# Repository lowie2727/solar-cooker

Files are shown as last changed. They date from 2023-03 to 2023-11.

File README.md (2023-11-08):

# Solar cooker

This repository contains the [arduino code](arduino) and [pcb layout](kicad) for the testing station of our solar cooker.

# Contributing

This repository is no longer actively maintained. If you want to contribute to this project, you can always fork this repository.

# Final result

This is the test station built by the first generation of electronics students.

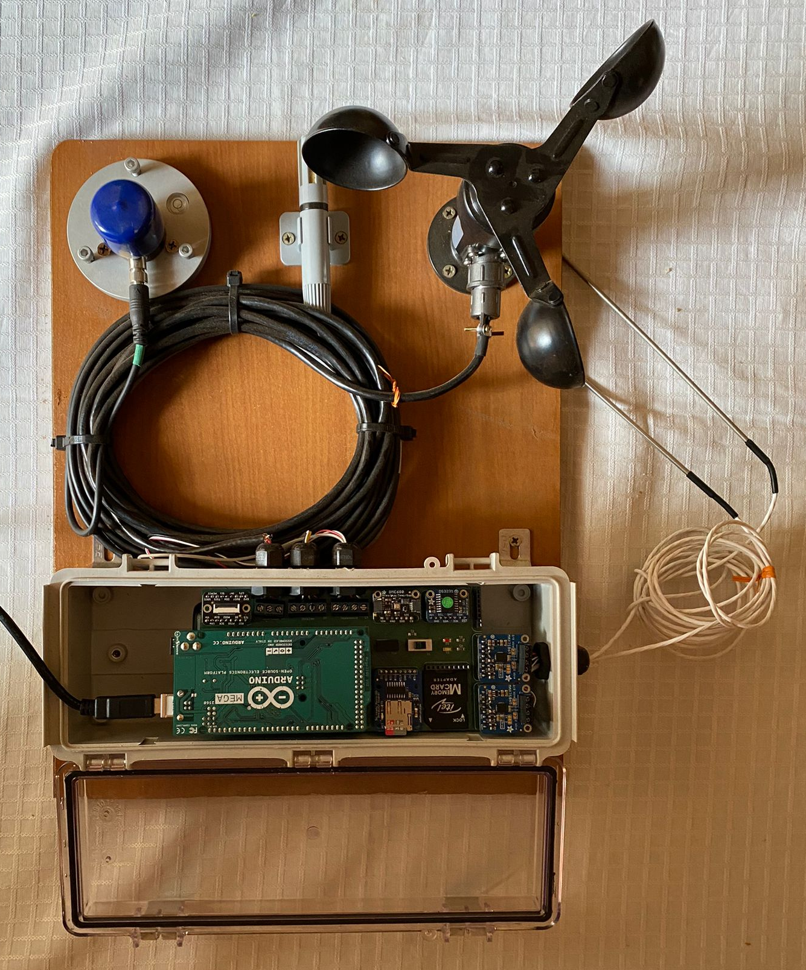
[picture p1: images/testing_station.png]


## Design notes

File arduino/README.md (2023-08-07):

# Arduino

The [**src**](src) folder contains the code for both the individual components and the code for the entire testing station.

The folder [**src/main**](src/main) contains the various components brought together. Each component has its own cpp file except for the LCD screen and microSD module. It is joined via header files in [main.cpp](src/main/main.cpp).

In the [**src/components**](src/components) subfolder, you will find code for each individual component, along with the connection diagram.

## PlatformIO

We migrated from the [Arduino IDE](https://www.arduino.cc/en/software) to [PlatformIO](https://platformio.org/platformio-ide) because of the size of the project.

### Prerequisites

#### Visual Studio Code

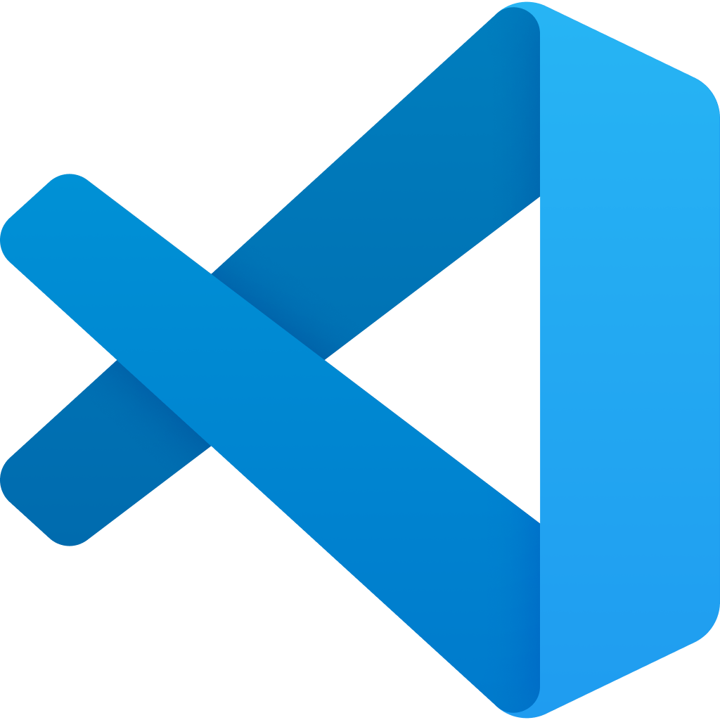
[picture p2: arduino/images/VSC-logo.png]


To use PlatformIO u need to first install [Visual Studio Code](https://code.visualstudio.com/)

When VSCode is installed you need to install the [PlatformIO extension](https://platformio.org/install/ide?install=vscode) in VSCode and then you are ready to compile. It may take some time so be patient.

#### Copy the project to your computer

To copy the project to your local machine you can download this [zip](https://github.com/lowie2727/solar-cooker/archive/refs/heads/main.zip) or if you have git installed you can run the `git clone https://github.com/lowie2727/solar-cooker.git` in a folder of your choice. Git is recommended to get the latest updates to the project.

### Using PlatformIO

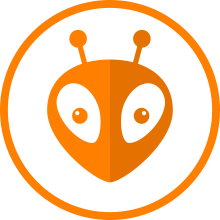
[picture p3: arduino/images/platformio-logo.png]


#### Opening the PlatformIO project

When the extension is successfully installed, you will get a new icon on the left in VSCode. Click on it and open the correct folder (open the folder with the platform.ini file assuming you already have a local copy of the project on your computer). In this case open the [arduino](/arduino) folder.

#### Build main

You will now see several project tasks when you click on the PlatformIO logo, open main and click on build. The terminal will open, if everything worked out it should show SUCCESS when it is done.

#### Upload and Monitor

To upload the code and view the serial monitor, a button is provided.

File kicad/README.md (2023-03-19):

# KiCad

## Installation

please install the latest kicad version from [kicad.org](https://www.kicad.org/download/)

## CADLAB (visual version control)
View this project on [CADLAB.io](https://cadlab.io/project/26616)

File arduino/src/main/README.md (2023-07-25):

# Main

## CSV

CSV files are generated in the following folder structure: YYYY/MM/DDHHMMSS.csv

the header of the CSV file looks like this:

| Year | Month | Day | Hour | Minute | Second | Outside temperature [°C] | Wind speed [m/s] | Air pressure (inside box) [hPa] | Relative humidity (inside box) [%] | Temperature inside pot 1 [°C] | Temperature inside pot 2 [°C] | Temperature inside pot 3 [°C] | Solar irradiance [W/m²] |
|---|---|-----|---|---|---|---|---|---|---|---|---|---|---|

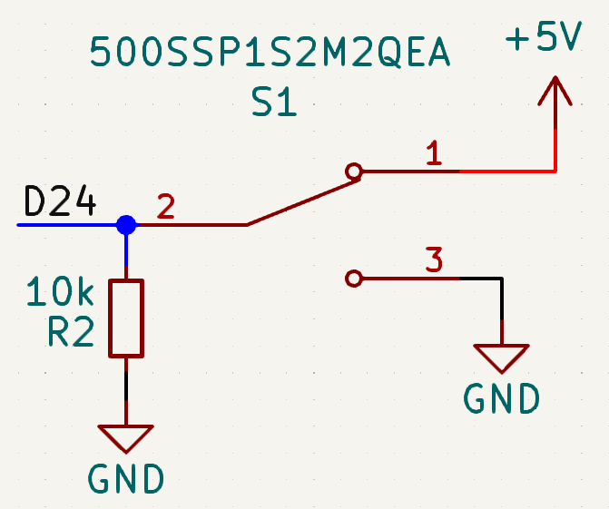
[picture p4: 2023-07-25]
arduino/src/components/switch/images/pinout_switch.png

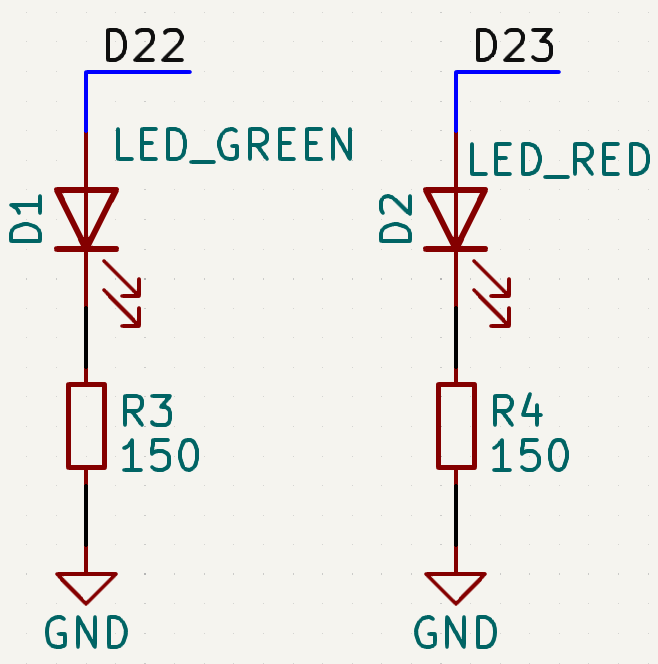
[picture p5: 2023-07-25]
arduino/src/components/switch/images/pinout_LED.png

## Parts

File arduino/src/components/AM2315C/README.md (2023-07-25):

# Sources

- [learn.adafruit.com](https://learn.adafruit.com/adafruit-aht20)

# Dependencies

- [Adafruit AHTX0](https://github.com/adafruit/Adafruit_AHTX0)

# Schematic

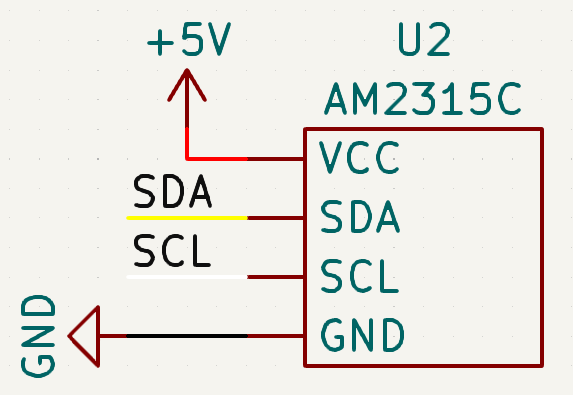
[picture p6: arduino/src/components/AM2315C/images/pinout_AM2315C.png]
pinout


## I2C

| Pin | Uno | Mega |
| --- | --- | ---- |
| SDA | SDA | 20 |
| SCL | SCL | 21 |

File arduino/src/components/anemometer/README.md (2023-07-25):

# Sources

- [wiki.dfrobot.com](https://wiki.dfrobot.com/Wind_Speed_Sensor_Voltage_Type_0-5V__SKU_SEN0170)

# Schematic

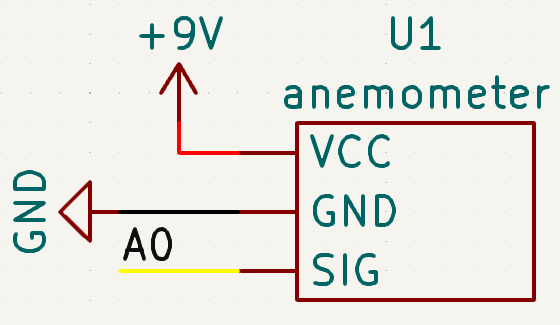
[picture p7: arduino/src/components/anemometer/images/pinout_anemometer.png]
pinout


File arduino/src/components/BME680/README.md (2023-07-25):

# Sources

- [learn.adafruit.com](https://learn.adafruit.com/adafruit-bme680-humidity-temperature-barometic-pressure-voc-gas)

# Dependencies

- [Adafruit BME680 Library](https://github.com/adafruit/Adafruit_BME680)

# Schematic

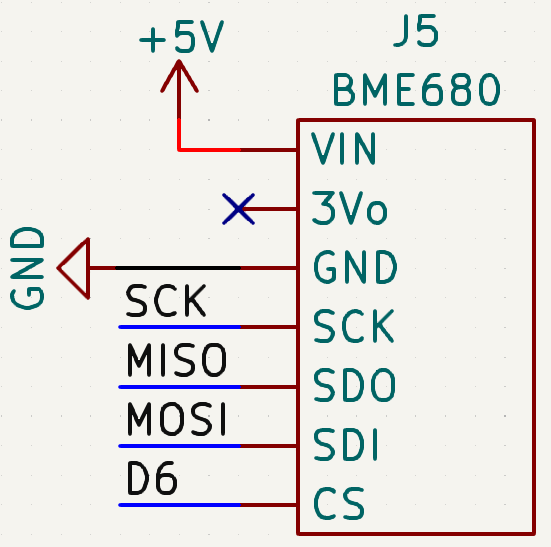
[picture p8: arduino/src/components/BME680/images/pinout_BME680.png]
pinout


## SPI

| Pin  | Uno | Mega |
| ---- | --- | ---- |
| MISO | 11  | 50 |
| MOSI | 12  | 51 |
| SCK  | 13  | 52 |

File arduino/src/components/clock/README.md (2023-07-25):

# Sources

- [learn.adafruit.com](https://learn.adafruit.com/adafruit-ds3231-precision-rtc-breakout)

# Dependencies

- [RTClib](https://github.com/adafruit/RTClib)

# Schematic

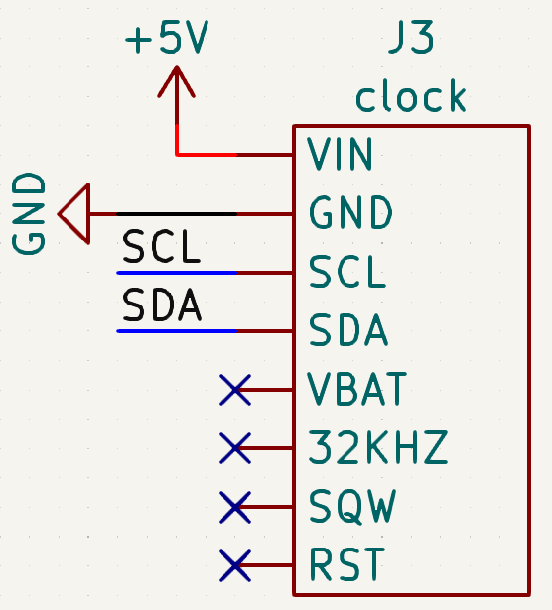
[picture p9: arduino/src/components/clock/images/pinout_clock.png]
pinout


## I2C

| Pin | Uno | Mega |
| --- | --- | ---- |
| SDA | SDA | 20 |
| SCL | SCL | 21 |

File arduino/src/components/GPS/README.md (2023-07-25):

# Sources

- [learn.adafruit.com](https://learn.adafruit.com/adafruit-ultimate-gps)

# Dependencies

- [Adafruit GPS Library](https://github.com/adafruit/Adafruit_GPS)

# Schematic

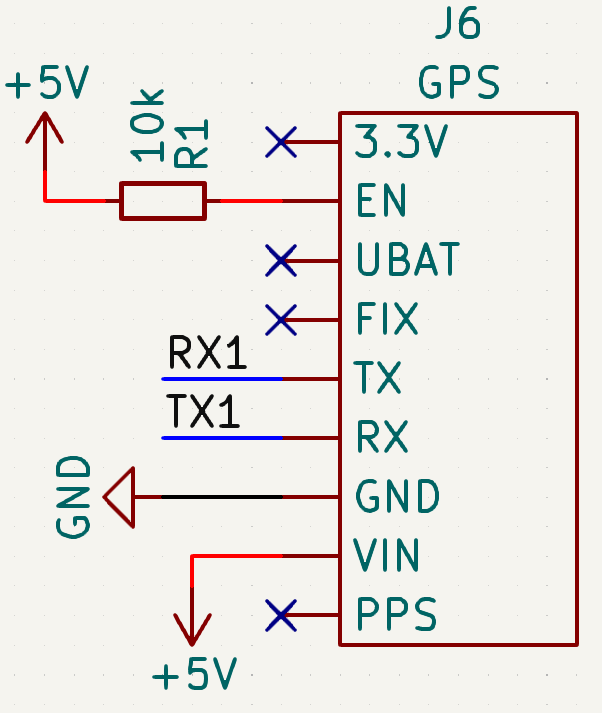
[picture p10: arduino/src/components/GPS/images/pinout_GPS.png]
pinout


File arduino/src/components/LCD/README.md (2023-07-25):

# Sources

- [learn.adafruit.com](https://learn.adafruit.com/2-2-tft-display)

# Dependencies

- [Adafruit ILI9341](https://github.com/adafruit/Adafruit_ILI9341)

# Schematic

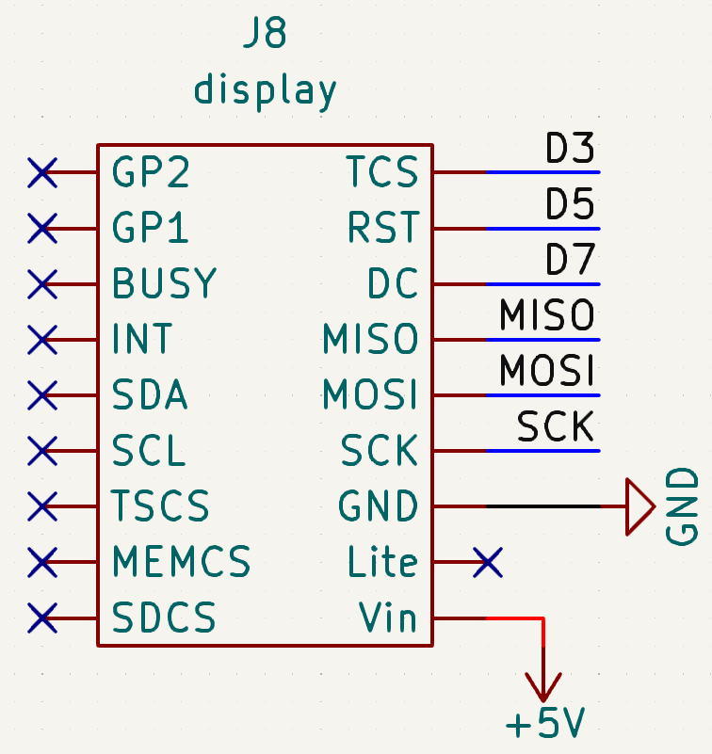
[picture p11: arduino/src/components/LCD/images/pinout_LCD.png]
pinout


## SPI

| Pin  | Uno | Mega |
| ---- | --- | ---- |
| MISO | 11  | 50 |
| MOSI | 12  | 51 |
| SCK  | 13  | 52 |

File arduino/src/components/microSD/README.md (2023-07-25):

# Sources

- [learn.adafruit.com](https://learn.adafruit.com/adafruit-micro-sd-breakout-board-card-tutorial)

# Dependencies

- [SdFat](https://github.com/greiman/SdFat)

# Schematic

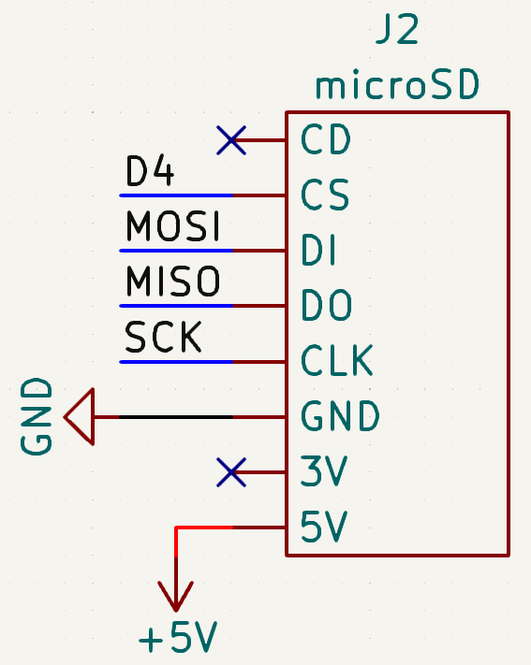
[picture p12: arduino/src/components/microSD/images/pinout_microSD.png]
pinout


## SPI

| Pin  | Uno | Mega |
| ---- | --- | ---- |
| MISO | 11  | 50 |
| MOSI | 12  | 51 |
| SCK  | 13  | 52 |

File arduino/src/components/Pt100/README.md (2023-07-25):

# Sources

- [learn.adafruit.com](https://learn.adafruit.com/adafruit-max31865-rtd-pt100-amplifier)

# Dependencies

- [Adafruit MAX31865 library](https://github.com/adafruit/Adafruit_MAX31865)

# Schematic

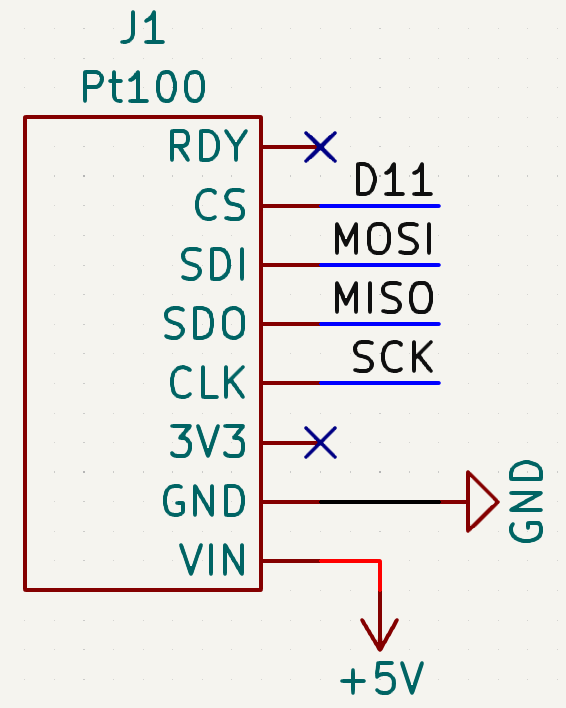
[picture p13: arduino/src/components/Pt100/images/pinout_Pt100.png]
pinout


## SPI

| Pin  | Uno | Mega |
| ---- | --- | ---- |
| MISO | 11  | 50 |
| MOSI | 12  | 51 |
| SCK  | 13  | 52 |

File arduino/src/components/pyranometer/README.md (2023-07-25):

# Sources

- [apogeeinstruments.com](https://www.apogeeinstruments.com/sp-215-ss-amplified-0-5-volt-pyranometer)

# Schematic

pinout

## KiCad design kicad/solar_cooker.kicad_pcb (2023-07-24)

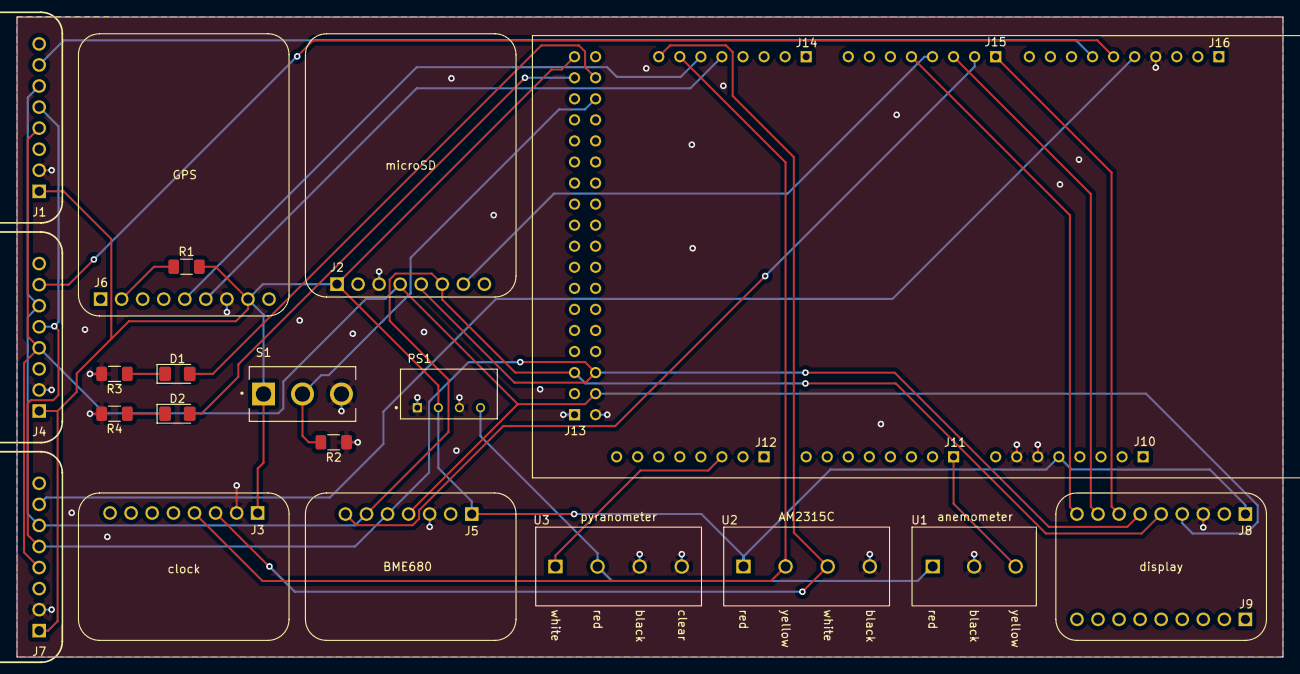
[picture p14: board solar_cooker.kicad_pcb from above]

Board: 2 copper layers, 152.7 x 77.2 mm, 20 parts (1 on the bottom side), 26 nets.

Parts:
A1: A000067; ARDUINO_A000067
D1: LED_GREEN; LED_1206_3216Metric_Pad1.42x1.75mm_HandSolder
D2: LED_RED; LED_1206_3216Metric_Pad1.42x1.75mm_HandSolder
J1, J4, J7: Pt100
J2: microSD
J3: clock
J5: BME680
J6: GPS
J8: display
PS1: TBA_1-0519; CONV_TBA_1-0519
R1, R2: 10k; R_1206_3216Metric_Pad1.30x1.75mm_HandSolder
R3, R4: 150; R_1206_3216Metric_Pad1.30x1.75mm_HandSolder
S1: 500SSP1S2M2QEA; SW_500SSP1S2M2QEA
U1: anemometer; screw_terminal_3pin
U2: AM2315C; screw_terminal_4pin
U3: pyranometer; screw_terminal_4pin

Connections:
+5V: A1.5V_1 (+5V_1), A1.5V_3 (+5V_3), J1.1 (VIN), J2.1 (5V), J3.1 (VIN), J4.1 (VIN), J5.1 (VIN), J6.8 (VIN), J7.1 (VIN), J8.1 (Vin), PS1.2 (+VIN(VCC)), R1.2, S1.1, U2.1 (VCC)
+9V: PS1.4 (+VOUT), U1.1 (VCC), U3.2 (VCC)
/A0: A1.AD0, U1.3 (SIG)
/A10: A1.AD10, U3.1 (SIG)
/D3: A1.3, J8.9 (TCS)
/D4: A1.4, J2.7 (CS)
/D5: A1.5, J8.8 (RST)
/D6: A1.6, J5.7 (CS)
/D7: A1.7, J8.7 (DC)
/D11: A1.11, J1.7 (CS)
/D12: A1.12, J4.7 (CS)
/D13: A1.13, J7.7 (CS)
/D22: A1.22, D1.2 (A)
/D23: A1.23, D2.2 (A)
/D24: A1.24, R2.2, S1.2
/MISO: A1.50, J1.5 (SDO), J2.5 (DO), J4.5 (SDO), J5.5 (SDO), J7.5 (SDO), J8.6 (MISO)
/MOSI: A1.51, J1.6 (SDI), J2.6 (DI), J4.6 (SDI), J5.6 (SDI), J7.6 (SDI), J8.5 (MOSI)
/RX1: A1.19, J6.5 (TX)
/SCK: A1.52, J1.4 (CLK), J2.4 (CLK), J4.4 (CLK), J5.4 (SCK), J7.4 (CLK), J8.4 (SCK)
/SCL: A1.21, J3.3 (SCL), U2.3 (SCL)
/SDA: A1.20, J3.4 (SDA), U2.2 (SDA)
/TX1: A1.18, J6.6 (RX)
GND: A1.GND1, A1.GND2, A1.GND3, A1.GND4, A1.GND5, J1.2 (GND), J2.3 (GND), J3.2 (GND), J4.2 (GND), J5.3 (GND), J6.7 (GND), J7.2 (GND), J8.3 (GND), PS1.1 (-VIN(GND)), PS1.3 (-VOUT), R2.1, R3.2, R4.2, S1.3, U1.2 (GND), U2.4 (GND), U3.3 (GND), U3.4 (GND)
unnamed: D1.1 (K), R3.1
unnamed: D2.1 (K), R4.1
unnamed: J6.2 (EN), R1.1

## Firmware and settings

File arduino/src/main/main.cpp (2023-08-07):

#include <Arduino.h>

#include "anemometer.h"

#include "AM2315C.h"

#include "BME680.h"

#include "clock.h"

#include "Pt100.h"

#include "pyranometer.h"

#include "switch.h"

// LCD
void LCDSetup();

#include "Adafruit_GFX.h"
#include "Adafruit_ILI9341.h"
#include "SPI.h"

#define TFT_DC 7
#define TFT_CS 3
#define TFT_RST 5

Adafruit_ILI9341 tft = Adafruit_ILI9341(TFT_CS, TFT_DC, TFT_RST);

void writeLine1();
void writeLine2();
void writeLine3();
void writeLine4();
void writeLine5();
void writeLine6();
void writeLine7();
void writeLine8();
void writeLine9();

char previousLine1[100];
char previousLine2[100];
char previousLine3[100];
char previousLine4[100];
char previousLine5[100];
char previousLine6[100];
char previousLine7[100];
char previousLine8[100];
char previousLine9[100];

float previousTemp = -1;
float previousHumidity = -1;
float previousPt100Temp1 = -1;
float previousPt100Temp2 = -1;
float previousPt100Temp3 = -1;
uint8_t previousSecond = -1;
float previousWind = -1;
float previousSolarIrradiance = -1;
float previousSlope = -1;

void writeDataToScreen();

unsigned long previousMillisScreen = 0;

// SD
#include <SdFat.h>

const int chipSelect = 4;

SdFat sd;
SdFile myFile;

char filePath[200];
int fileNameUpdated = 0;
unsigned long previousMillisSD = 0;

void updateFileName();
void makeFile();

void microSDSetup();
void writeCSVHeaders();
void writeDataToSD();

float tempBuffer[60];
int bufferIndex = 0;
int isArrayEmpty = 1;

void shiftAndAppend(float array[], float value);
void initArray(float array[], float value);

unsigned long testDurationMillis = 0;

void setup() {
  Serial.begin(9600);
  while (!Serial) {
  }
  Serial.println();

  AM2315CSetup();
  anemoSetup();
  BME680Setup();
  clockSetup();
  microSDSetup();
  Pt100Setup();
  pyranoSetup();
  switchSetup();
  LCDSetup();
}

void loop() {
  if (getSwitchState()) {
    greenLedOn();

    if (!fileNameUpdated) {
      testDurationMillis = millis();
      updateFileName();
      writeCSVHeaders();
      fileNameUpdated = 1;
    }

    unsigned long currentMillisScreen = millis();

    if (currentMillisScreen - previousMillisScreen >= 1000) {
      writeDataToScreen();
      previousMillisScreen = currentMillisScreen;
    }

    unsigned long currentMillisSD = millis();

    if (currentMillisSD - previousMillisSD >= 10000) {
      writeDataToSD();
      previousMillisSD = currentMillisSD;
    }
  } else {
    redLedOn();
    fileNameUpdated = 0;
    isArrayEmpty = 1;
  }
}

void microSDSetup() {
  if (!sd.begin(chipSelect, SPI_FULL_SPEED)) {
    sd.initErrorHalt();
  }
}

void writeCSVHeaders() {
  char CSVHeaders[] =
      "Year;Month;Day;Hour;Minute;Second;Outside temperature "
      "[°C];Wind speed [m/s];Air pressure (inside box) [hPa];Relative humidity "
      "(inside box) [%];Temperature inside pot 1 [°C];Temperature inside pot 2 "
      "[°C];Temperature inside pot 3 [°C];Solar irradiance [W/m²]";
  if (!myFile.open(filePath, O_RDWR | O_CREAT | O_AT_END)) {
    sd.errorHalt(F("opening test.txt for write failed"));
  }
  Serial.println("Writing CSV headers");
  myFile.println(CSVHeaders);
  myFile.close();
  Serial.println(F("done writing."));
}

void writeDataToSD() {
  char AM2315CTemp[30];
  dtostrf(getAM2315CTemp(), 4, 2, AM2315CTemp);

  char AM2315CHum[20];
  dtostrf(getAM2315CHum(), 5, 2, AM2315CHum);

  char BME680Humidity[20];
  dtostrf(getBME680Humidity(), 6, 2, BME680Humidity);

  char BME680Pressure[20];
  dtostrf(getBME680Pressure(), 6, 2, BME680Pressure);

  char BME680Temperature[20];
  dtostrf(getBME680Temperature(), 6, 2, BME680Temperature);

  char windSpeed[20];
  dtostrf(getWindSpeed(), 4, 2, windSpeed);

  char Pt100Temp1[20];
  if (!getPt100Fault_1()) {
    dtostrf(getPt100Temp1(), 5, 2, Pt100Temp1);
  } else {
    snprintf(Pt100Temp1, 20, "x");
  }

  char Pt100Temp2[20];
  if (!getPt100Fault_2()) {
    dtostrf(getPt100Temp2(), 5, 2, Pt100Temp2);
  } else {
    snprintf(Pt100Temp2, 20, "x");
  }

  char Pt100Temp3[20];
  if (!getPt100Fault_3()) {
    dtostrf(getPt100Temp3(), 5, 2, Pt100Temp3);
  } else {
    snprintf(Pt100Temp3, 20, "x");
  }

  char solarIrradiance[20];
  dtostrf(getSolarIrradiance(), 6, 2, solarIrradiance);

  char dataSd[500];
  snprintf(dataSd, 500, "%04d;%02d;%02d;%02d;%02d;%02d;%s;%s;%s;%s;%s;%s;%s;%s",
           getYear(), getMonth(), getDay(), getHour24(), getMinute(),
           getSecond(), AM2315CTemp, windSpeed, BME680Pressure, AM2315CHum,
           Pt100Temp1, Pt100Temp2, Pt100Temp3, solarIrradiance);

  if (!myFile.open(filePath, O_RDWR | O_CREAT | O_AT_END)) {
    sd.errorHalt(F("opening test.txt for write failed"));
  }
  Serial.println(dataSd);
  myFile.println(dataSd);
  myFile.close();
  Serial.println(F("done writing."));
}

void updateFileName() {
  snprintf(filePath, 200, "%04d/%02d/%02d%02d%02d%02d.csv", getYear(),
           getMonth(), getDay(), getHour24(), getMinute(), getSecond());

  Serial.println(filePath);

  char dirName[200];
  snprintf(dirName, 200, "%04d/%02d/", getYear(), getMonth());

  sd.mkdir(String(getYear()));
  sd.mkdir(dirName);

  makeFile();
}

void makeFile() {
  if (!myFile.open(filePath, O_RDWR | O_CREAT | O_AT_END)) {
    sd.errorHalt("opening file for write failed");
  }
  myFile.close();
}

void LCDSetup() {
  tft.begin();
  tft.fillScreen(ILI9341_BLACK);
}

void writeDataToScreen() {
  writeLine1();
  writeLine2();
  writeLine3();
  writeLine4();
  writeLine5();
  writeLine6();
  writeLine7();
  writeLine8();
  writeLine9();
}

void writeLine1() {
  unsigned long currentTestDurationSeconds =
      (unsigned long)(millis() - testDurationMillis) / 1000;

  uint8_t hours = currentTestDurationSeconds / 3600;

  int remainder1 = currentTestDurationSeconds % 3600;
  uint8_t minutes = remainder1 / 60;

  uint8_t seconds = remainder1 % 60;

  char line1[100];
  snprintf(line1, 100, "Time  : %02dh %02dm %02ds", hours, minutes, seconds);

  if (previousSecond != seconds) {
    previousSecond = seconds;
    tft.setCursor(0, 0);
    tft.setTextColor(ILI9341_BLACK);
    tft.setTextSize(2);
    tft.println(previousLine1);
    strcpy(previousLine1, line1);
    tft.setCursor(0, 0);
    tft.setTextColor(ILI9341_GREEN);
    tft.setTextSize(2);
    tft.println(line1);
  }
}

void writeLine2() {
  char line2[100];
  if (!getPt100Fault_1()) {
    float Pt100Temp1Float = getPt100Temp1();

    char Pt100Temp1[20];
    dtostrf(Pt100Temp1Float, 5, 2, Pt100Temp1);

    char line2[100];
    snprintf(line2, 100, "Pot 1 : %s C", Pt100Temp1);

    if (previousPt100Temp1 != Pt100Temp1Float) {
      previousPt100Temp1 = Pt100Temp1Float;
      tft.setCursor(0, 20);
      tft.setTextColor(ILI9341_BLACK);
      tft.setTextSize(2);
      tft.println(previousLine2);
      strcpy(previousLine2, line2);
      tft.setCursor(0, 20);
      tft.setTextColor(ILI9341_GREEN);
      tft.setTextSize(2);
      tft.println(line2);
    }
  } else {
    tft.setCursor(0, 20);
    tft.setTextColor(ILI9341_BLACK);
    tft.setTextSize(2);
    snprintf(line2, 100, "Pot 1 : NULL");
    tft.println(previousLine2);
    strcpy(previousLine2, line2);
    tft.setCursor(0, 20);
    tft.setTextColor(ILI9341_GREEN);
    tft.setTextSize(2);
    tft.println(line2);
  }
}

void writeLine3() {
  char line3[100];
  if (!getPt100Fault_2()) {
    float Pt100Temp2Float = getPt100Temp2();

    char Pt100Temp2[20];
    dtostrf(Pt100Temp2Float, 5, 2, Pt100Temp2);

    char line3[100];
    snprintf(line3, 100, "Pot 2 : %s C", Pt100Temp2);

    if (previousPt100Temp2 != Pt100Temp2Float) {
      previousPt100Temp2 = Pt100Temp2Float;
      tft.setCursor(0, 40);
      tft.setTextColor(ILI9341_BLACK);
      tft.setTextSize(2);
      tft.println(previousLine3);
      strcpy(previousLine3, line3);
      tft.setCursor(0, 40);
      tft.setTextColor(ILI9341_GREEN);
      tft.setTextSize(2);
      tft.println(line3);
    }
  } else {
    tft.setCursor(0, 40);
    tft.setTextColor(ILI9341_BLACK);
    tft.setTextSize(2);
    snprintf(line3, 100, "Pot 2 : NULL");
    tft.println(previousLine3);
    strcpy(previousLine3, line3);
    tft.setCursor(0, 40);
    tft.setTextColor(ILI9341_GREEN);
    tft.setTextSize(2);
    tft.println(line3);
  }
}

void writeLine4() {
  char line4[100];
  if (!getPt100Fault_3()) {
    float Pt100Temp3Float = getPt100Temp3();

    char Pt100Temp3[20];
    dtostrf(Pt100Temp3Float, 5, 2, Pt100Temp3);

    char line4[100];
    snprintf(line4, 100, "Pot 3 : %s C", Pt100Temp3);

    if (previousPt100Temp3 != Pt100Temp3Float) {
      previousPt100Temp3 = Pt100Temp3Float;
      tft.setCursor(0, 60);
      tft.setTextColor(ILI9341_BLACK);
      tft.setTextSize(2);
      tft.println(previousLine4);
      strcpy(previousLine4, line4);
      tft.setCursor(0, 60);
      tft.setTextColor(ILI9341_GREEN);
      tft.setTextSize(2);
      tft.println(line4);
    }
  } else {
    tft.setCursor(0, 60);
    tft.setTextColor(ILI9341_BLACK);
    tft.setTextSize(2);
    snprintf(line4, 100, "Pot 3 : NULL");
    tft.println(previousLine4);
    strcpy(previousLine4, line4);
    tft.setCursor(0, 60);
    tft.setTextColor(ILI9341_GREEN);
    tft.setTextSize(2);
    tft.println(line4);
  }
}

void writeLine5() {
  float wind = getWindSpeed();

  char windSpeed[20];
  dtostrf(getWindSpeed(), 4, 2, windSpeed);

  char line5[100];
  snprintf(line5, 100, "Wind  : %s m/s", windSpeed);

  if (previousWind != wind) {
    previousWind = wind;
    tft.setCursor(0, 80);
    tft.setTextColor(ILI9341_BLACK);
    tft.setTextSize(2);
    tft.println(previousLine5);
    strcpy(previousLine5, line5);
    tft.setCursor(0, 80);
    tft.setTextColor(ILI9341_GREEN);
    tft.setTextSize(2);
    tft.println(line5);
  }
}

void writeLine6() {
  float solarIrradianceFloat = getSolarIrradiance();

  char solarIrradiance[20];
  dtostrf(solarIrradianceFloat, 6, 2, solarIrradiance);

  char line6[100];
  snprintf(line6, 100, "Irr : %s W/m2", solarIrradiance);

  if (previousSolarIrradiance != solarIrradianceFloat) {
    previousSolarIrradiance = solarIrradianceFloat;
    tft.setCursor(0, 100);
    tft.setTextColor(ILI9341_BLACK);
    tft.setTextSize(2);
    tft.println(previousLine6);
    strcpy(previousLine6, line6);
    tft.setCursor(0, 100);
    tft.setTextColor(ILI9341_GREEN);
    tft.setTextSize(2);
    tft.println(line6);
  }
}

void writeLine7() {
  if (!getPt100Fault_1()) {
    float temp = getPt100Temp1();
    if (isArrayEmpty) {
      initArray(tempBuffer, temp);
      isArrayEmpty = 0;
    } else {
      shiftAndAppend(tempBuffer, temp);
    }
  }

  char slope[30];
  float slopeFloat = tempBuffer[59] - tempBuffer[0];
  dtostrf(slopeFloat, 4, 2, slope);

  char line7[100];
  snprintf(line7, 100, "Slope 1min: %sC", slope);

  if (previousSlope != slopeFloat) {
    previousSlope = slopeFloat;
    tft.setCursor(0, 120);
    tft.setTextColor(ILI9341_BLACK);
    tft.setTextSize(2);
    tft.println(previousLine7);
    strcpy(previousLine7, line7);
    tft.setCursor(0, 120);
    tft.setTextColor(ILI9341_GREEN);
    tft.setTextSize(2);
    tft.println(line7);
  }
}

void shiftAndAppend(float array[], float value) {
  for (size_t i = 0; i < 60 - 1; i++) {
    array[i] = array[i + 1];
  }
  array[60 - 1] = value;
}

void initArray(float array[], float value) {
  for (size_t i = 0; i < 60; i++) {
    array[i] = value;
  }
}

void writeLine8() {
  float temp = getAM2315CTemp();

  char AM2315CTemp[30];
  dtostrf(temp, 4, 2, AM2315CTemp);

  char line8[100];
  snprintf(line8, 100, "Temp out: %sC", AM2315CTemp);

  if (previousTemp != temp) {
    previousTemp = temp;
    tft.setCursor(0, 140);
    tft.setTextColor(ILI9341_BLACK);
    tft.setTextSize(2);
    tft.println(previousLine8);
    strcpy(previousLine8, line8);
    tft.setCursor(0, 140);
    tft.setTextColor(ILI9341_GREEN);
    tft.setTextSize(2);
    tft.println(line8);
  }
}

void writeLine9() {
  float AM2315CHumidityFloat = getAM2315CHum();

  char AM2315CHumidity[20];
  dtostrf(AM2315CHumidityFloat, 4, 2, AM2315CHumidity);

  char line9[100];
  snprintf(line9, 100, "Humidity: %s%%", AM2315CHumidity);

  if (previousHumidity != AM2315CHumidityFloat) {
    previousHumidity = AM2315CHumidityFloat;
    tft.setCursor(0, 160);
    tft.setTextColor(ILI9341_BLACK);
    tft.setTextSize(2);
    tft.println(previousLine9);
    strcpy(previousLine9, line9);
    tft.setCursor(0, 160);
    tft.setTextColor(ILI9341_GREEN);
    tft.setTextSize(2);
    tft.println(line9);
  }
}

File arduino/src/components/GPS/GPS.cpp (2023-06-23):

// Test code for Ultimate GPS Using Hardware Serial (e.g. GPS Flora or
// FeatherWing)
//
// This code shows how to listen to the GPS module via polling. Best used with
// Feathers or Flora where you have hardware Serial and no interrupt
//
// Tested and works great with the Adafruit GPS FeatherWing
// ------> https://www.adafruit.com/products/3133
// or Flora GPS
// ------> https://www.adafruit.com/products/1059
// but also works with the shield, breakout
// ------> https://www.adafruit.com/products/1272
// ------> https://www.adafruit.com/products/746
//
// Pick one up today at the Adafruit electronics shop
// and help support open source hardware & software! -ada

#include <Adafruit_GPS.h>

// what's the name of the hardware serial port?
#define GPSSerial Serial1

// Connect to the GPS on the hardware port
Adafruit_GPS GPS(&GPSSerial);

// Set GPSECHO to 'false' to turn off echoing the GPS data to the Serial console
// Set to 'true' if you want to debug and listen to the raw GPS sentences
#define GPSECHO false

uint32_t timer = millis();

void setup() {
  // while (!Serial);  // uncomment to have the sketch wait until Serial is
  // ready

  // connect at 115200 so we can read the GPS fast enough and echo without
  // dropping chars also spit it out
  Serial.begin(9600);
  Serial.println("Adafruit GPS library basic parsing test!");

  // 9600 NMEA is the default baud rate for Adafruit MTK GPS's- some use 4800
  GPS.begin(9600);
  // uncomment this line to turn on RMC (recommended minimum) and GGA (fix data)
  // including altitude
  GPS.sendCommand(PMTK_SET_NMEA_OUTPUT_RMCGGA);
  // uncomment this line to turn on only the "minimum recommended" data
  // GPS.sendCommand(PMTK_SET_NMEA_OUTPUT_RMCONLY);
  // For parsing data, we don't suggest using anything but either RMC only or
  // RMC+GGA since the parser doesn't care about other sentences at this time
  // Set the update rate
  GPS.sendCommand(PMTK_SET_NMEA_UPDATE_1HZ); // 1 Hz update rate
  // For the parsing code to work nicely and have time to sort thru the data,
  // and print it out we don't suggest using anything higher than 1 Hz

  // Request updates on antenna status, comment out to keep quiet
  GPS.sendCommand(PGCMD_ANTENNA);

  delay(1000);

  // Ask for firmware version
  GPSSerial.println(PMTK_Q_RELEASE);
}

void loop() // run over and over again
{
  // read data from the GPS in the 'main loop'
  char c = GPS.read();
  // if you want to debug, this is a good time to do it!
  if (GPSECHO)
    if (c)
      Serial.print(c);
  // if a sentence is received, we can check the checksum, parse it...
  if (GPS.newNMEAreceived()) {
    // a tricky thing here is if we print the NMEA sentence, or data
    // we end up not listening and catching other sentences!
    // so be very wary if using OUTPUT_ALLDATA and trying to print out data
    Serial.print(
        GPS.lastNMEA()); // this also sets the newNMEAreceived() flag to false
    if (!GPS.parse(GPS.lastNMEA())) // this also sets the newNMEAreceived() flag
                                    // to false
      return; // we can fail to parse a sentence in which case we should just
              // wait for another
  }

  // approximately every 2 seconds or so, print out the current stats
  if (millis() - timer > 2000) {
    timer = millis(); // reset the timer
    Serial.print("\nTime: ");
    if (GPS.hour < 10) {
      Serial.print('0');
    }
    Serial.print(GPS.hour, DEC);
    Serial.print(':');
    if (GPS.minute < 10) {
      Serial.print('0');
    }
    Serial.print(GPS.minute, DEC);
    Serial.print(':');
    if (GPS.seconds < 10) {
      Serial.print('0');
    }
    Serial.print(GPS.seconds, DEC);
    Serial.print('.');
    if (GPS.milliseconds < 10) {
      Serial.print("00");
    } else if (GPS.milliseconds > 9 && GPS.milliseconds < 100) {
      Serial.print("0");
    }
    Serial.println(GPS.milliseconds);
    Serial.print("Date: ");
    Serial.print(GPS.day, DEC);
    Serial.print('/');
    Serial.print(GPS.month, DEC);
    Serial.print("/20");
    Serial.println(GPS.year, DEC);
    Serial.print("Fix: ");
    Serial.print((int)GPS.fix);
    Serial.print(" quality: ");
    Serial.println((int)GPS.fixquality);
    if (GPS.fix) {
      Serial.print("Location: ");
      Serial.print(GPS.latitude, 4);
      Serial.print(GPS.lat);
      Serial.print(", ");
      Serial.print(GPS.longitude, 4);
      Serial.println(GPS.lon);
      Serial.print("Speed (knots): ");
      Serial.println(GPS.speed);
      Serial.print("Angle: ");
      Serial.println(GPS.angle);
      Serial.print("Altitude: ");
      Serial.println(GPS.altitude);
      Serial.print("Satellites: ");
      Serial.println((int)GPS.satellites);
      Serial.print("Antenna status: ");
      Serial.println((int)GPS.antenna);
    }
  }
}

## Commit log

2023-03-14 added outside temperature sensor and microSD card
2023-03-14 added KiCad project
    [solar_cooker.kicad_pcb, solar_cooker.kicad_sch]
2023-03-15 added custom microSD component
    [solar_cooker.kicad_sch]
2023-03-15 added clockModule
    [solar_cooker.kicad_sch]
2023-03-16 kicad project update
    [solar_cooker.kicad_pcb, solar_cooker.kicad_sch]
2023-03-19 added e-Paper + minor improvements
    [solar_cooker.kicad_sch]
2023-03-20 e-Paper printing variable that changes
2023-03-20 files are generated based on the current time
2023-03-21 arduino workflow
2023-03-22 Arduino CLI implementation
2023-03-22 arduino workflow update
2023-03-27 update arduino main README.md + formatting
2023-03-30 added switch
2023-03-30 anemometer + switch schematic
    [solar_cooker.kicad_sch]
2023-03-31 schematic and documentation update
    [solar_cooker.kicad_sch]
2023-04-04 added PT100
    [solar_cooker.kicad_sch]
2023-04-07 update main
    added switch with red and green leds, starting measurements with the switch creates new file
2023-04-10 added GPS schematic
    [solar_cooker.kicad_sch]
2023-04-10 GPS schematic update
    [solar_cooker.kicad_sch]
2023-04-10 added KiCad v2
    work in progress
    [solar_cooker.kicad_pcb, solar_cooker.kicad_sch, solar_cooker_v2.kicad_pcb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]
2023-04-10 KiCad v2 update
    [solar_cooker.kicad_sch, solar_cooker_v2.kicad_pcb, solar_cooker_v2.kicad_sch]
2023-04-11 update main + added schematic AM2315
    [solar_cooker.kicad_sch]
2023-05-01 kicad update
    [arduino.kicad_sch, sensors.kicad_sch, solar_cooker_v2.kicad_sch]
2023-05-02 added KiCad v1.5 + workflow improvement
    [solar_cooker_v1.5.kicad_pcb, solar_cooker_v1.5.kicad_sch]
2023-05-03 update csv headers + file name fix
    [main.cpp, microSD.cpp]
2023-05-05 added Arduino Mega KiCad
    [solar_cooker_v1.5.kicad_pcb, solar_cooker_v1.5.kicad_sch]
2023-05-05 pcb has now 3 pt100 sensors
    [solar_cooker_v1.5.kicad_pcb, solar_cooker_v1.5.kicad_sch]
2023-05-07 added GPS to pcb
    [solar_cooker_v1.5.kicad_pcb, solar_cooker_v1.5.kicad_sch]
2023-05-07 routing update
    [solar_cooker_v1.5.kicad_pcb, solar_cooker_v1.5.kicad_sch]
2023-05-07 added DC-DC converter
    [solar_cooker_v1.5.kicad_sch]
2023-05-07 converter scheme and footprint added
    [solar_cooker_v1.5.kicad_pcb, solar_cooker_v1.5.kicad_sch]
2023-05-08 drc fix
    [solar_cooker_v1.5.kicad_pcb, solar_cooker_v1.5.kicad_sch]
2023-05-08 added display
    [solar_cooker_v1.5.kicad_pcb, solar_cooker_v1.5.kicad_sch]
2023-05-08 added display connections
    [solar_cooker_v1.5.kicad_sch]
2023-05-08 routed display
    [solar_cooker_v1.5.kicad_pcb]
2023-05-08 added gps connections
    [solar_cooker_v1.5.kicad_pcb, solar_cooker_v1.5.kicad_sch]
2023-05-09 updated display connections
    [solar_cooker_v1.5.kicad_sch]
2023-05-09 conflict removed
    [solar_cooker_v1.5.kicad_sch]
2023-05-09 rerouted display and gps
    [solar_cooker_v1.5.kicad_pcb, solar_cooker_v1.5.kicad_sch]
2023-05-14 updatet pcb
    [solar_cooker_v1.5.kicad_pcb, solar_cooker_v1.5.kicad_sch]
2023-05-14 pcb minor fix
    [solar_cooker_v1.5.kicad_pcb]
2023-05-16 silkscreen fix for order v1
    [solar_cooker_v1.5.kicad_pcb, solar_cooker_v1.5.kicad_sch]
2023-05-28 gps fix
    [solar_cooker_v1.5.kicad_sch]
2023-05-29 kicad structure improvement
    [arduino.kicad_sch, sensors.kicad_sch, solar_cooker.kicad_pcb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]
2023-06-05 fixed GPS and clock module in kicad
    [solar_cooker_v1.5.kicad_pcb, solar_cooker_v1.5.kicad_sch]
2023-06-06 footprints update
    [solar_cooker_v1.5.kicad_pcb]
2023-06-08 all footprints ready
    [solar_cooker_v1.5.kicad_pcb, solar_cooker_v1.5.kicad_sch]
2023-06-08 PCB routing and footprints done
    [solar_cooker_v1.5.kicad_pcb]
2023-06-08 silkscreen update
    [solar_cooker_v1.5.kicad_pcb]
2023-06-08 structure improvement kicad + added connectors
    [solar_cooker_v1.5.kicad_pcb, solar_cooker_v1.5.kicad_sch]
2023-06-09 bom generation from schematic
    [solar_cooker_v1.5.kicad_pcb, solar_cooker_v1.5.kicad_sch]
2023-06-09 arduino mega footprint update + 3D view added
    [solar_cooker_v1.5.kicad_pcb]
2023-06-09 minor silkscreen fix
    [solar_cooker_v1.5.kicad_pcb, solar_cooker_v1.5.kicad_sch]
2023-06-09 minor update silkscreen
    [solar_cooker_v1.5.kicad_pcb]
2023-06-09 order v2
    [solar_cooker_v1.5.kicad_pcb, solar_cooker_v1.5.kicad_sch]
2023-06-09 BOM generation update
    now uses KiBoM
    [solar_cooker_v1.5.kicad_pcb, solar_cooker_v1.5.kicad_sch]
2023-06-10 project files rename + connector improvement
    [connectors.kicad_sch, solar_cooker.kicad_pcb, solar_cooker.kicad_sch]
2023-06-10 Electrical Rules Checker fix
    there are still some issues that need to be resolved
    [connectors.kicad_sch, solar_cooker.kicad_pcb, solar_cooker.kicad_sch]
2023-06-20 kicad 9V DCDC convertor Vout- fix + rename clock
    [solar_cooker.kicad_pcb, solar_cooker.kicad_sch]
2023-06-20 microSD module fix kicad
    MISO and MOSI flipped
    [solar_cooker.kicad_pcb, solar_cooker.kicad_sch]
2023-06-23 new anemometer code fix
    [AM2315C.cpp, anemometer.cpp]
2023-06-23 GPS code change + minor fixes
    [BME680.cpp, GPS.cpp, Pt100.cpp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]
2023-06-27 arduino display update in main (still broken)
    writing to file not possible when using display
    AM2315C still buggy (faulty sensor)
    not all sensor data visible on screen yet
    [AM2315C.cpp, BME680.cpp, Pt100.cpp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]
2023-07-12 updated 3D model kicad
    [solar_cooker.kicad_pcb]
2023-07-19 fixed some display mistakes and finished slow function
    [main.cpp]
2023-07-19 test.cpp 3 Pt100 sensors update
2023-07-22 KiCad 3D view update
    [solar_cooker.kicad_pcb]
2023-07-22 Arduino README.md update
2023-07-22 KiCad README.md update
2023-07-24 silkscreen update + schematic improvements
    [solar_cooker.kicad_pcb, solar_cooker.kicad_sch]
